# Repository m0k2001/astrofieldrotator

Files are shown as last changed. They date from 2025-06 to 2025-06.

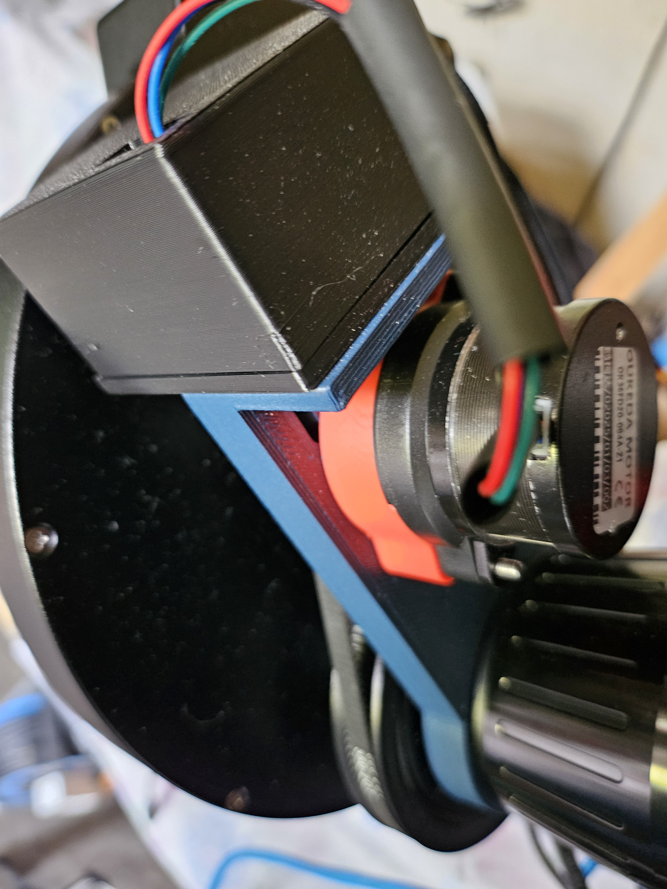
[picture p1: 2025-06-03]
IMG/20250603_150844.jpg

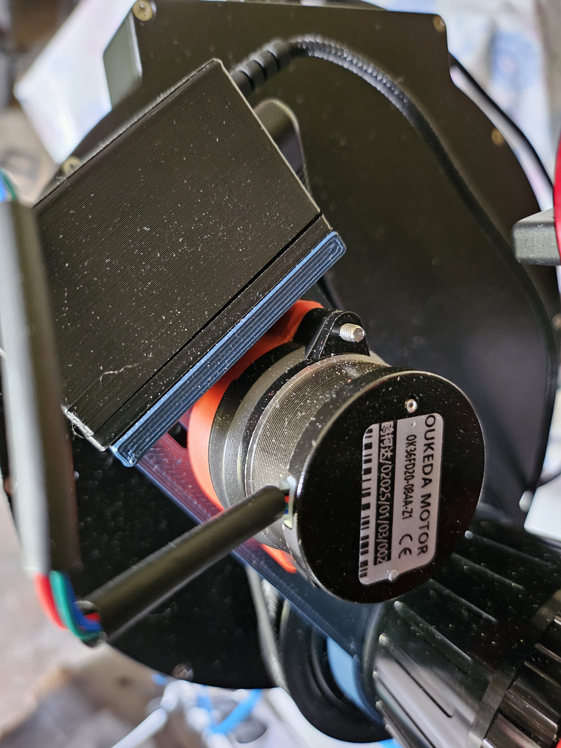
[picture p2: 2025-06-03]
IMG/20250603_150852.jpg

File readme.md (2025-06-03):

Remix from different projects :

https://www.scopefocus.info/home/rotator
<br>
https://www.thingiverse.com/thing:5253710
<br>
https://www.thingiverse.com/thing:5243794
<br>

You can use different motor options. 2 PCB and box heights if you solder Arduino Nano board directly on PCB or if you use pin headers to keep it removable.
Backfocus length is about 25mm.
It works perfectly fine with [ASCOM driver](https://drive.google.com/file/d/1Zqj4HnF0sWtz7hacBCAIt85_bKwMDyPM/view?usp=drive_web) (I personnaly use [N.I.N.A](https://nighttime-imaging.eu/) flawlessly).
Ther's also a [Windows App](https://drive.google.com/file/d/1RpfXV0fqB5MPrnLDqRJleW-3eae0BWBA/view?usp=drive_web) to test teh device.

I improved some details :
- better/stronger holding of the ring
- PCB box
- PCB design :
    - added a microswicth to reverse rotation (Arduino must be restarted for change to be effective)
    - added an optional DC buck converter to power Arduino Nano
    - different motor/pulley options
    - increased GT2 ring : 144 teeth
    - Arduino formware : MS1, MS2, MS3 are software defined. Rotation speed/acceleration modified.
- added M48 and M54 design compatibility

BOM Electronics :
- Arduino Nano (chinese clone works well)
- [Green A4988 Stepper Driver](https://fr.aliexpress.com/item/1005006096236486.html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) Please take care to finely adjust Vref according to motor model : 0,85V for NEMA 17 HS4401, 0,56V for NEMA 17HS08 and NEMA 14 (Galileo 2 kit)
- (optional) [Female 2.54 Breakable Pin Header Connector Strip](https://fr.aliexpress.com/item/32993182990.html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)
- [JST XH 4pins female for PCB](https://fr.aliexpress.com/item/1005003422202370.html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)
- [5,5/2,1 DC Plug](https://fr.aliexpress.com/item/32872192541.html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)
- [Mini Switch SPDT](https://fr.aliexpress.com/item/4000042632226.html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)
- [Electrolytic capacitor 100uF - 16v minimum](https://fr.aliexpress.com/item/1005005558643765.html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)
- [(optional) Buck Converter 9V](https://fr.aliexpress.com/item/1005007342634171.html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)
- USB cable
- DC 5.5/2.1 12V Power Source if needed

BOM Motion :
- Stepper Motor (3 otpions):
    - [NEMA 17 42mm or 44mm](https://fr.aliexpress.com/item/1005001303445983.html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)
    - [NEMA 17 pancake](https://fr.aliexpress.com/item/1005005742670433.html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)
    - [Galileo 2 extruder kit](https://fr.aliexpress.com/item/1005007811125592.html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)
- [6mm GT2 Belt 348mm or 350mm](https://fr.aliexpress.com/item/1005003420210494.html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)
- [Rotation ring (42, 48 or 54mm)](https://fr.aliexpress.com/item/33018620597.html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)
- [GT2 pulley - W6B5 - 16 or 20 teeth](https://fr.aliexpress.com/item/1005001933418605.html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)
- [M2.53 Brass Inserts OD 3.5 Length 4mm](https://fr.aliexpress.com/item/1005004535859664.html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)
- [M2 Brass Inserts OD 3.2 Length 3mm](https://fr.aliexpress.com/item/1005003582355741.html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)
- M2, M2.5 and M3 screws, M3 washers
- Square Nut M3 5mm

Tools :
- 3D Printer (I recommend at least ABS/ASA, but PETG-CF is way more rigid - PLA is not suitable)
- Solder Iron
- Arduino IDE to flash [firmware](https://github.com/m0k2001/astrofieldrotator/tree/main/Arduino/ArduinoRotatorFirmware_ver1008_switch)
- Multimeter

Her is a summary of different motor options (steps per degree is a parameter you must define in ASCOM driver options) :
| Motor model | 17HS08-1004S | 17HS08-1004S | 17HS4001 | 17HS4001 | Nema36 + Planetary  |
|---|---|---|---|---|---|
| Pulley Teeth | 16 | 20 | 16 | 20 | 20 |
| Torque (N.cm) | 144 | 115 | 378 | 302 | 648 |
| Rel. motor thickness | 0 | 0 | + 20mm | + 20mm | + 18mm |
| Steps / degree | 80 | 64 | 80 | 64 | 576 |
| Precision (degre) | 1/5 | 1/4 | 1/5 | 1/4 | 1/36 |
| Precision (arcsec) | 720 | 900 | 720 | 900 | 100 |
| Price | + | + | + | + | ++ |

Using planetary gearbox NEMA 36 and 54mm rotation ring should not cost more than 120€, without 3D printing and power source.

Just to give a comparison, Zwo CAA is 399€, 25 N.cm torque, precision < 0,1° ( < 360 arcsec). But thickness is less important (17,5mm).

Have fun !

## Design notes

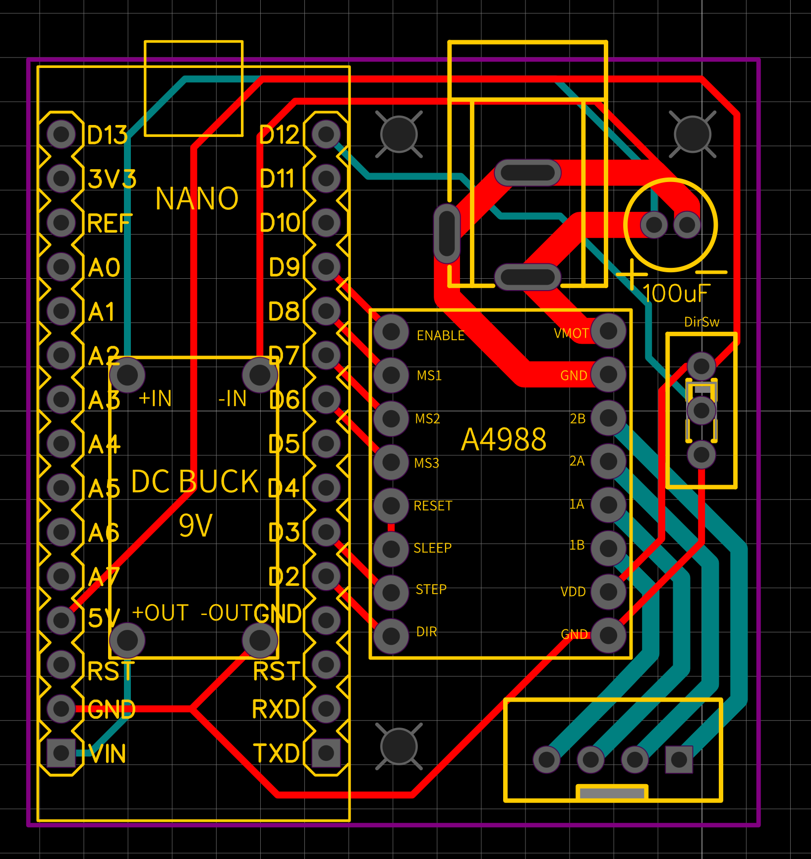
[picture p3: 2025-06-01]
PCB/PCB_circuit.png

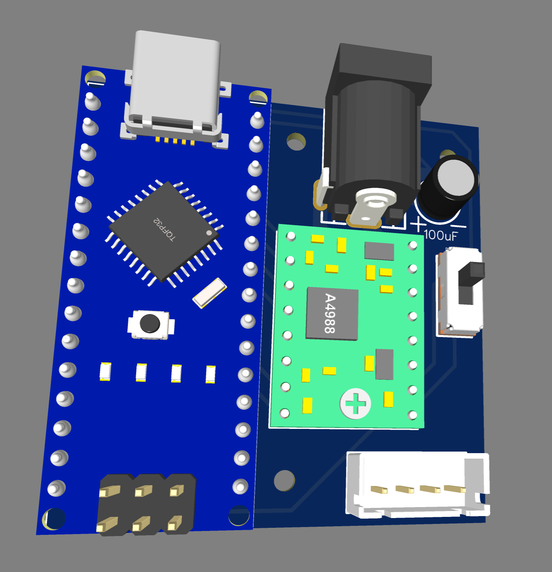
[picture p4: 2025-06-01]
PCB/PCB_3D.png

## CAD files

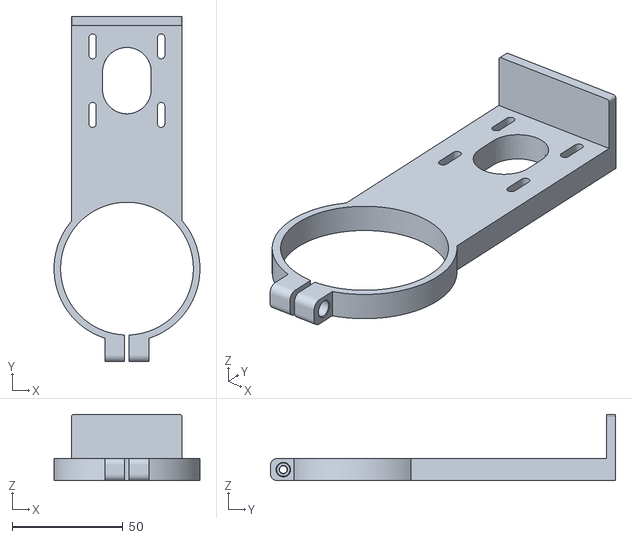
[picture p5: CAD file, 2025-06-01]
STL/Galileo 2/Rotateur_corps_M54_G2.stl
66.0 x 156.0 x 30.0

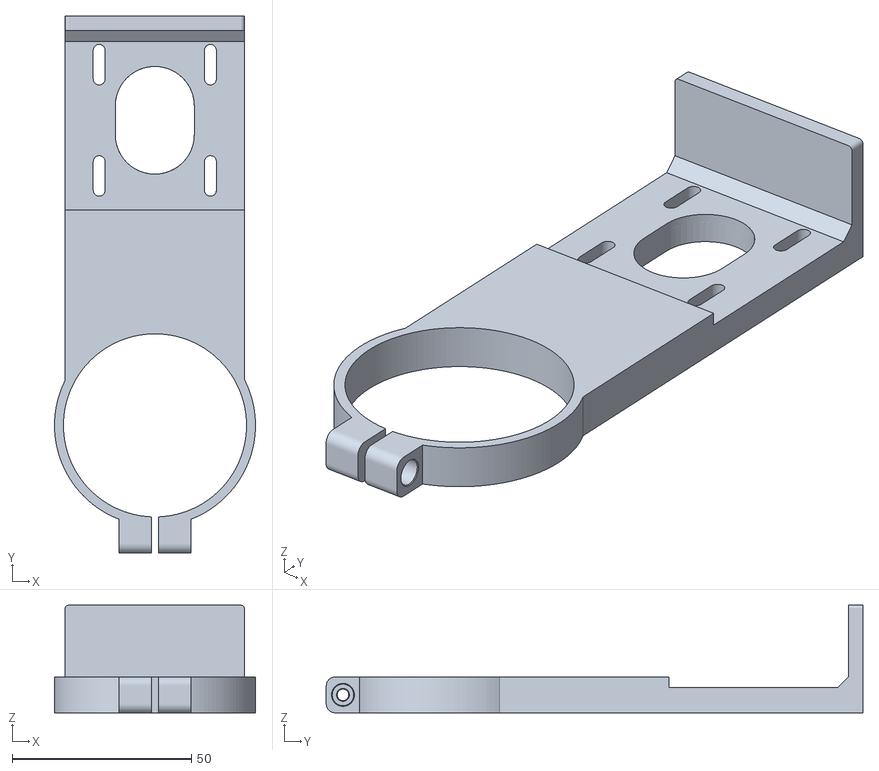
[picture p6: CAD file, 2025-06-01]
STL/NEMA 17/Rotateur_corps_M48.stl
56.0 x 149.5 x 30.0

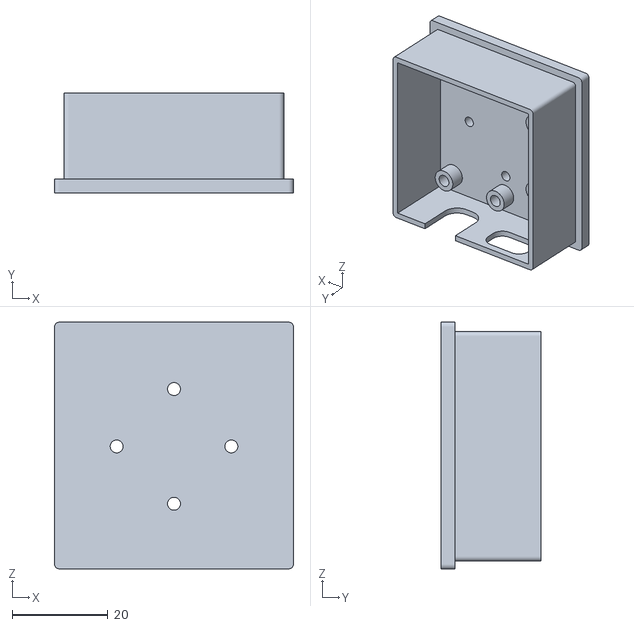
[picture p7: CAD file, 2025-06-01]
STL/PCB Box/Slim/Rotator_box_slim.stl
50.0 x 21.0 x 51.6

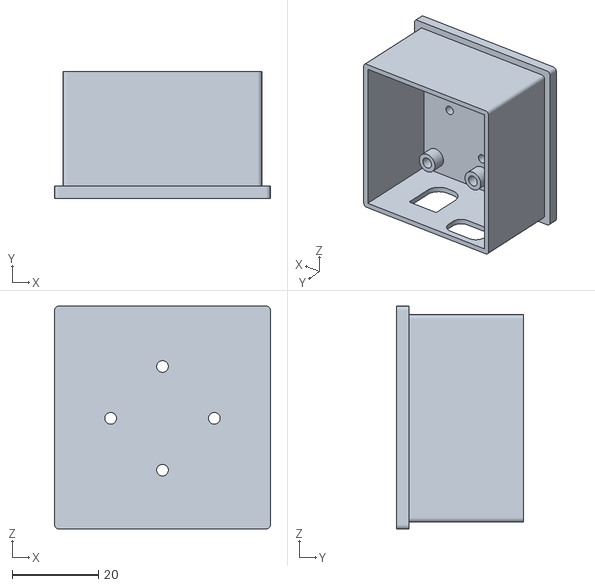
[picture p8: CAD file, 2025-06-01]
STL/PCB Box/Standard/Rotator_box_standard.stl
50.0 x 29.5 x 51.6

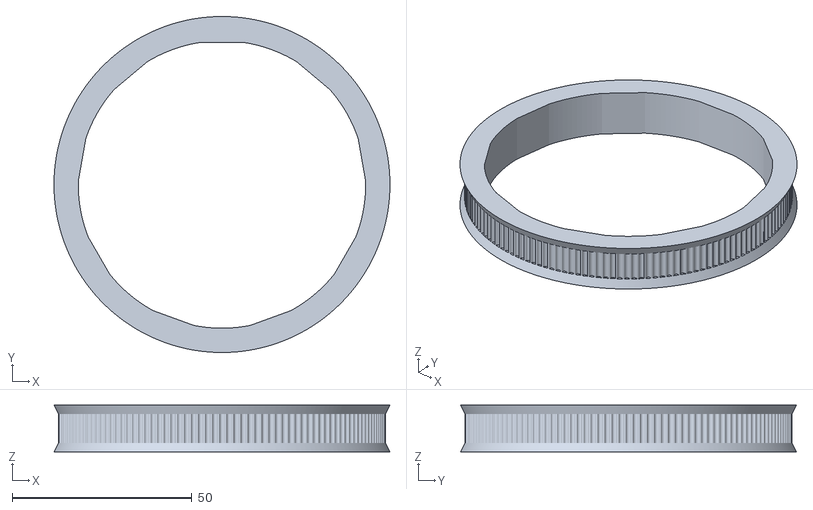
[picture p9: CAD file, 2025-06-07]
STL/Ring/M54 Wheel.stl
93.5 x 93.5 x 13.0

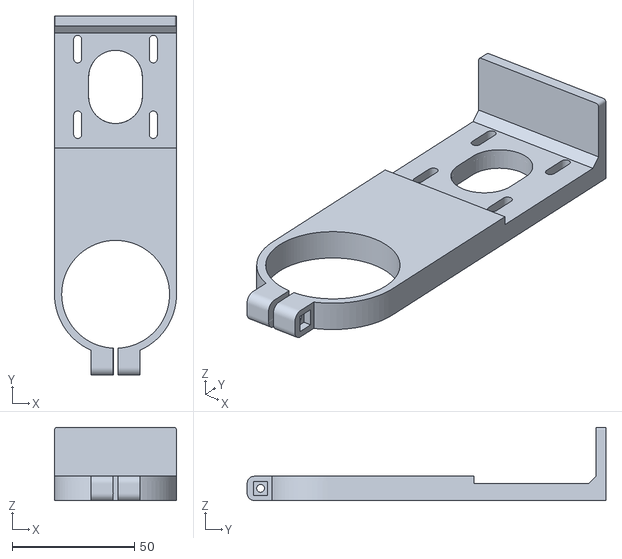
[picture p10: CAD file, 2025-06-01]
STL/NEMA 17/Rotateur_corps_M42.stl
50.0 x 147.0 x 30.0

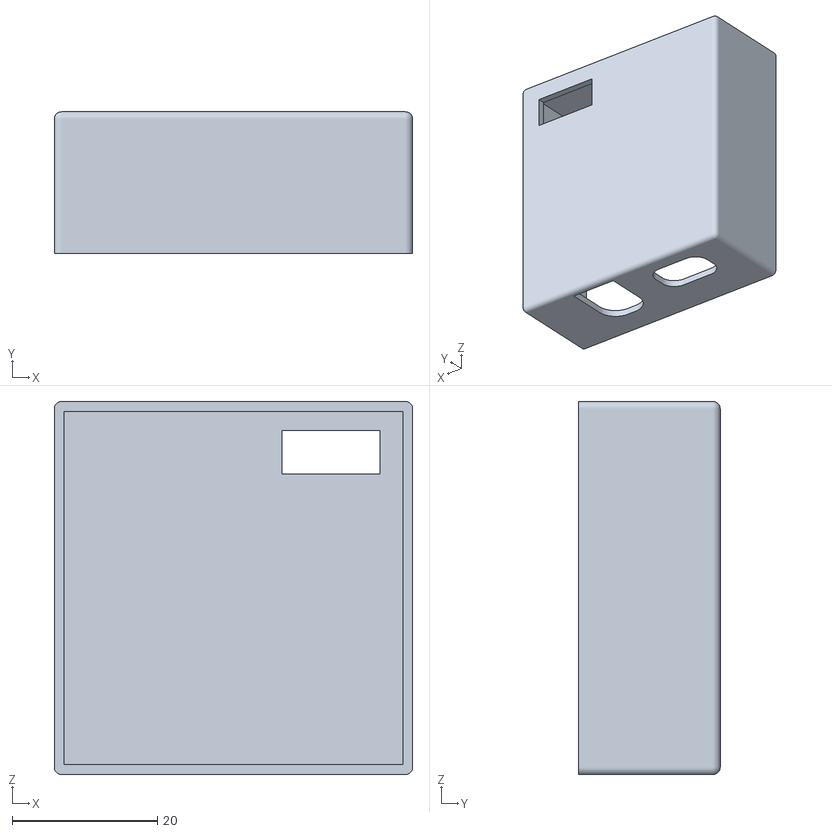
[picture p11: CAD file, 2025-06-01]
STL/PCB Box/Slim/Rotator_cover_slim.stl
49.4 x 19.5 x 51.4

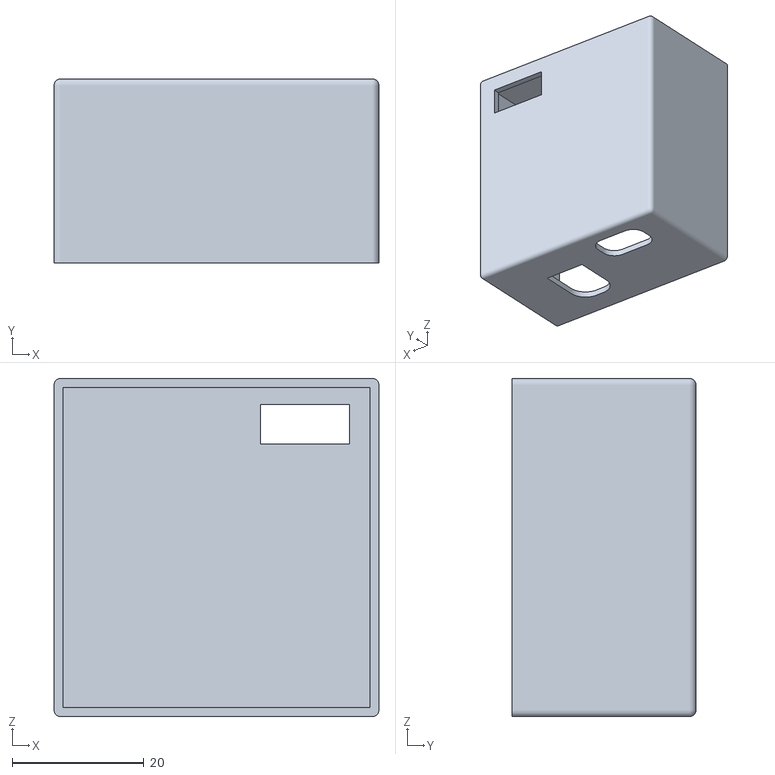
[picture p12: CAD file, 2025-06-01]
STL/PCB Box/Standard/Rotator_cover_standard.stl
49.4 x 28.0 x 51.4

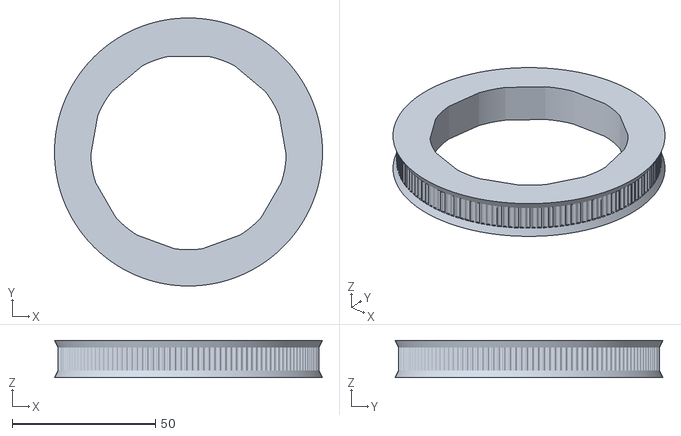
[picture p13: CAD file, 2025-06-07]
STL/Ring/M42 Wheel.stl
93.5 x 93.5 x 13.0

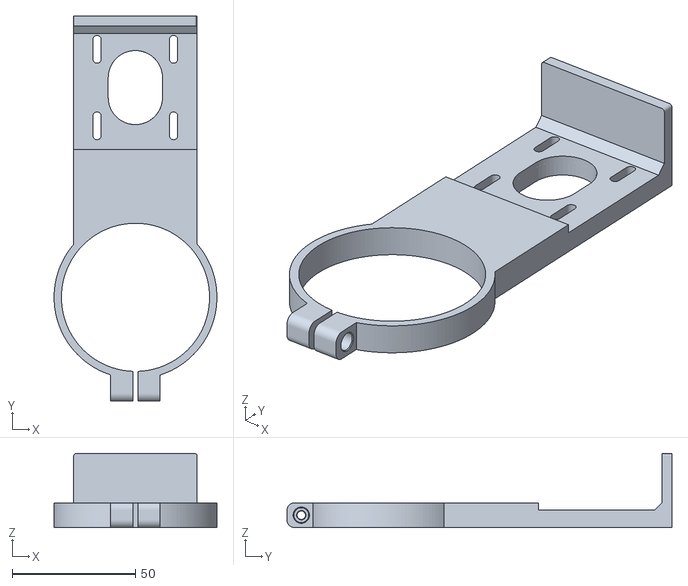
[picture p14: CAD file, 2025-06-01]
STL/NEMA 17/Rotateur_corps_M54.stl
66.0 x 156.0 x 30.0

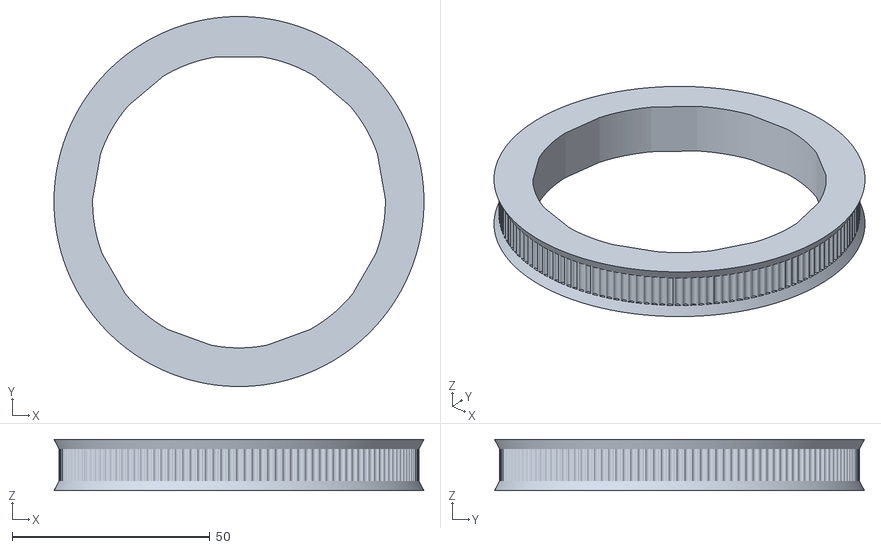
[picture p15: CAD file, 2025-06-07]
STL/Ring/M48 Wheel.stl
93.5 x 93.5 x 13.0

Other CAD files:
STL/Galileo 2/Rotateur_corps_M48_G2.stl

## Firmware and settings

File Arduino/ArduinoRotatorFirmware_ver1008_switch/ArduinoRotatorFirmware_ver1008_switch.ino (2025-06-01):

#include <AccelStepper.h>
#include <EEPROM.h>
#define DirectionPin 2
#define PulsePin 3
#define EnablePin 9
#define gear 9
#define microsteps 16

#define DEVICE_RESPONSE "scopfocus Rotator ver 1008"
int ver = 1008;
// EEPROM addresses
#define FOCUSER_POS_START 0
#define STEPPER_SPEED_ADD 3

AccelStepper stepper(1, PulsePin, DirectionPin);  //(mode, stepPin, directionPin)

// Global vars
boolean hold = false;
boolean reversed;
boolean positionSaved;  // Flag indicates if stepper position was saved as new focuser position
boolean firstPrint = false;
String inputString;  // Serial input command string (terminated with \n)

// *************  this value must be changed for each specific setup ***************************************
long maxSteps = 46080*gear;  // **** steps needed for 2 complete revolutions.  prevent cord wrap.
//  Must also enter this value/720 = steps/degree for first time ASCOM driver setup, click "properties
// ******************************************************************************************************

//int manualMoveStepSize = 50;  //higher number for faster manual moves
//int findHomeStepSize = 100; //adjusts finding home speed

int HEState = 0;
long lastDebounceTime = 0;
//  int counter = 0;
long debounceDelay = 20;

void loop() {
  // Stepper loop
  digitalWrite(EnablePin, LOW);
  if (stepper.distanceToGo() == 0 && !positionSaved) {
    saveFocuserPos(stepper.currentPosition());
    positionSaved = true;
  }
  if (stepper.distanceToGo() != 0 && !firstPrint) {
    firstPrint = true;
    Serial.print("P ");
    Serial.print(stepper.targetPosition());  //currentPosition() no accurate until move is done  **** was println, changes w/ adding # below
    Serial.print(";");
    Serial.print("M ");
    Serial.print("true");  //true
    Serial.println("#");
  }

  stepper.run();
}

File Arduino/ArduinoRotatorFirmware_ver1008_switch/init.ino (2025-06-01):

// Initialization routine
#define DirectionPin 2
#define PulsePin 3
#define EnablePin 9
#define MS1Pin 8
#define MS2Pin 7
#define MS3Pin 6
#define ReversePin 12

void setup() {
  pinMode(PulsePin, OUTPUT);
  digitalWrite(PulsePin, LOW);
  pinMode(DirectionPin, OUTPUT);
  digitalWrite(DirectionPin, LOW);
  pinMode(EnablePin, OUTPUT);
  digitalWrite(EnablePin, LOW);
  pinMode(MS1Pin, OUTPUT);
  pinMode(MS2Pin, OUTPUT);
  pinMode(MS3Pin, OUTPUT);

  switch (microsteps) {
    case 16:
    {
      digitalWrite(MS1Pin, HIGH);
      digitalWrite(MS2Pin, HIGH);
      digitalWrite(MS3Pin, HIGH);
      break;
    }
    case 8:
    {
      digitalWrite(MS1Pin, HIGH);
      digitalWrite(MS2Pin, HIGH);
      digitalWrite(MS3Pin, LOW);
      break;
    }
    case 4:
    {
      digitalWrite(MS1Pin, LOW);
      digitalWrite(MS2Pin, HIGH);
      digitalWrite(MS3Pin, LOW);
      break;
    }
    case 2:
    {
      digitalWrite(MS1Pin, HIGH);
      digitalWrite(MS2Pin, LOW);
      digitalWrite(MS3Pin, LOW);
      break;
    }
    case 1:
    {
      digitalWrite(MS1Pin, LOW);
      digitalWrite(MS2Pin, LOW);
      digitalWrite(MS3Pin, LOW);
      break;
    }

    
  }

  pinMode(ReversePin, INPUT);

  // Initialize serial
  Serial.begin(9600);
  Serial.setTimeout(2000);

  // Initialize stepper motor
  stepper.setMaxSpeed(gear*2500);     // 5000 works good,  use 500000 for confrom test1000 geared rotator10000 for geared stepper   200 for non-geared large stepper(500 max)  also may depend on what else is on loop()
  stepper.setAcceleration(gear*500);  //1000 for geared rotator  10000 for geared stepper    1000 for non-geared large stepper
  stepper.setCurrentPosition(readFocuserPos());
  positionSaved = true;
  inputString = "";
  Serial.print("ASCOM.Arduino.Rotator ");
  Serial.println("ver 1.0.0.8");
  reverseDir(digitalRead(ReversePin));  // reverseDir(digitalRead(!ReversePin));      // if NO SWITCH soldered and if you need to reverse rotation
  Serial.print("Pos = ");
  Serial.println(stepper.currentPosition());
}

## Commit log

2025-06-01 STL+Gerber+Arduino added
    [Rotateur_corps_M42.stl, Rotateur_corps_M48.stl, Rotateur_corps_M48_G2.stl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]
2025-06-07 Ajout STL roues
    [M42 Wheel.stl, M48 Wheel.stl, M54 Wheel.stl]
